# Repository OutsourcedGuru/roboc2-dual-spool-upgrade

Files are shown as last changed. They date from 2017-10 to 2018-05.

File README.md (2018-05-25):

# roboc2-dual-spool-upgrade
Step-by-step instructions for upgrading the Robo C2 for dual filament spools.



## Overview

The Robo C2 printer is awesome in many ways. Its included spool holder, however, has a number of flaws in its design:

* The mounting hole for the spool holder is slightly too large for the included holders, resulting in the holder spinning inside the rectangular hole and sometimes falling out mid-print
* The included holder for 1KG spools really isn't up to the challenge of all that weight
* The holders, as supplied, often catch against Robo's own filament spools given the existing design
* The location of the existing spool holder is too high and too close to the bottom of the filament run-out switch assembly, exacerbating any cross-filament problems and especially with infused rolls

To work around these flaws, I've created a completely new design to accommodate two 1KG spools at once.

The new design includes ball bearings, moves the spool(s) lower, re-orients them so that they're more inline with the filament run-out switch assembly and has a safety feature which helps on Shaxon and other problematically-wound filament spools.

I've decided to create two versions of the holder to include a second *smaller* version to hold two half-KG of filament. The only real difference between the two in printed parts are the lengths of the sleeves and the Under-brackets. And obviously, they use slightly longer dowels. If you like making these, double the amount of ball bearings and bolts and you should be able to make both models easily with the same materials otherwise.

### Follow-up project
Soon enough, I plan to create an enclosure for this dual-spool assembly to keep both spools dry since I intend to print PVA on the second extruder.

## Parts required
I've included pictures below to make this easier.

### Parts to order/buy
* Four non-flanged ball bearings, 8mm ID x 22mm OD, around $1.99 per pair, for [example](https://www.servocity.com/8mm-id-x-22mm-od-non-flanged-ball-bearing)
* Two types of dowel
	* 7/8" x 36", around $3.59 each at arts & crafts stores, for [example](https://www.whiteheadindustrial.com/p-20143-78-x-36-hardwood-dowel-rod-code-brown-no-301621.aspx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)
	* 3/16" x 36", around $0.79 each at arts & crafts stores, for [example](https://www.c2f.com/html/productdetail.asp?p=MID-7905)
* Several types of #6-32 shouldered aluminum bolts, around $1.69 for quantity 25 each for [example](https://www.servocity.com/6-32-zinc-plated-socket-head-machine-screws), or something like [this](https://www.servocity.com/actobotics-hardware-pack-a) would be a better idea
	* 7/16" (11.11mm) @ eight each
	* 1/2" (12.72mm) @ four each
	* 1/4" (6.35) @ two each
* Four or eight soft furniture stick-ons for the bottom
* A 7/64ths hex wrench for tightening all the bolts
* A hammer
* A pocketknife or similar
* A wood or hack saw

ball-bearings

dowel_7-8ths-inch-x-36-inch

dowel_3-16ths-inch-x-36-inch

bolt-6-32_7-16ths

hexkey-7-64ths

### Parts to print
Here's the part list, all in PLA. I used the standard [Robo 3D Jet Black](http://robo.fyi/consumables/filament-by-type-by-vendor) for all the parts.

#### Dual KG version:

1. **RC_DualSpool-1of4(PrintTwice).gcode** x 2 => two **Center Axis Brackets**, two **Center Axis Covers** and four **End Caps**
2. **RC_DualSpool-2of4(PrintOnceKG).gcode** x 1 => two **Assembly** parts and four **Sleeves**
3. **RC_DualSpool-3of4(PrintTwiceKG).gcode** x 2 => two halves of the **Under-brackets** and two **Mid-shims**
4. **RC_DualSpool-4of4(PrintTwiceKG).gcode** x 2 => two halves of the remaining **Under-brackets**

#### Dual Half-KG version:

1. **RC_DualSpool-1of4(PrintTwice).gcode** x 2 => two **Center Axis Brackets**, two **Center Axis Covers** and four **End Caps**
2. **RC_DualSpool-2of4(PrintOnceHalfKG).gcode** x 1 => two **Assembly** parts and four **Sleeves**
3. **RC_DualSpool-3of4(PrintTwiceHalfKG).gcode** x 2 => two halves of the **Under-brackets** and two **Mid-shims**

#### Note
Given that the Robo C2 has a fair degree of inaccuracy when printing Z-oriented holes, it's important for you to print these parts using the GCODE I've provided; otherwise, your bolts won't fit. (I've already factored in the hole-shrinkage in this dimension.)

* Assembly x 2
* End Cap x 4
* Mid-shim x 2 (needs raft & support)
* Sleeve x 4 *{Note that there is a shorter pair for the half-KG version of this project so choose appropriately}*
* Center Axis Bracket x 2
* Center Axis Cover x 2
* Under-bracket (both halves, needs raft & support) x 2 *{Note that there is a shorter pair for the half-KG version of this project so choose appropriately}*

## Installation
After printing all the parts, here are the assembly instructions.

1. Do a test-fit to determine if the **End Caps** fit into the ball bearings; that the 3/16" dowel fits inside the **Sleeves**, **End Caps** and **Mid-shims**; that the #6-32 bolts fit into the threaded holes and fit through the clean ones
2. Use the pocketknife to clean the upper half of the ball bearing slots in both **Assembly** parts
3. Insert one ball bearing each into the related slots in both **Assembly** parts, use a spare raft or other thin plastic part on top of this and use the hammer to gently force them into the back of each hole
4. Add one **End Cap** to each ball bearing
5. Insert the 3/16" dowel into one of the **End Cap** & ball bearing combinations
6. Onto this, thread in this order: one **Sleeve**, one **Mid-shim**, another **Sleeve** and another **End Cap** (with the opposite orientation as the last)
7. Pushing everything together, mark the point where the dowel clears the last part and cut the dowel
8. Repeat for the other ball bearing
9. Sandwich everything together with another **Assembly** part on the opposite side
10. Match up the correct pairs of **Under-brackets**, aligning the holes on the bottom, use two 7/16" bolts to attach them together
11. Flip everything upside-down and begin attaching the combined **Under-brackets** using the four 1/2" bolts... if necessary, carefully use the hammer to set the **Assembly** parts evenly into the rectangular grooves in the **Under-bracket** parts, tighten each bolt firmly
12. Verify that all four sleeves spin freely
13. Add four cushioned furniture bumpers/feet to the bottom to protect your table top
14. Use the 1/4" bolts to attach one each **Center Axis Cover** to the **Center Axis Brackets** (don't over-tighten)
15. Use two each 7/16" bolts to attach both **Center Axis Brackets** to their respective Assembly part, tightening them firmly
16. Close one **Center Axis Cover**, insert the 7/16" dowel through everything and mark a line 2mm inside (the depth of the other **Center Axis Cover**), saw through the dowel
17. Orient the dual-spool holder behind the printer and add two filament spools so that the filament spools clockwise as seen from the right side of the printer, slide the dowel through the middle and close both covers, slightly tightening their bolts by hand

testfit

bottomaxles





sideview-c2andholder



|Donate||Cryptocurrency|
|:-----:|---|:---:|
| eth-receive || btc-receive |
|Ethereum||Bitcoin|

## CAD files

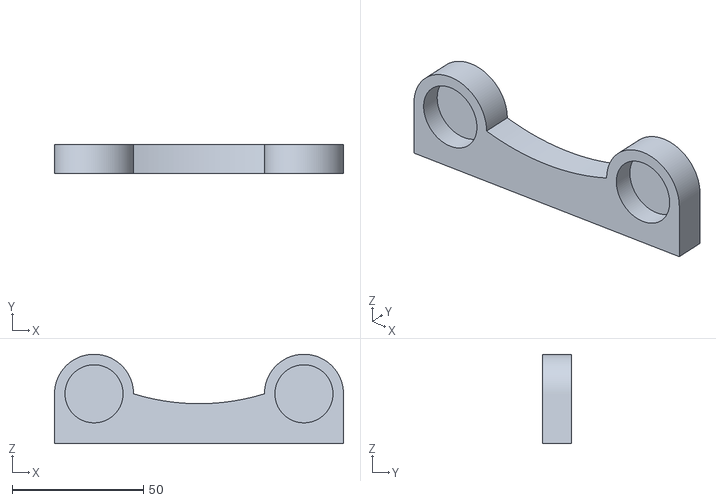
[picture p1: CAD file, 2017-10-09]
parts/stl/DualSpool-Assembly.stl
110.0 x 11.0 x 34.0

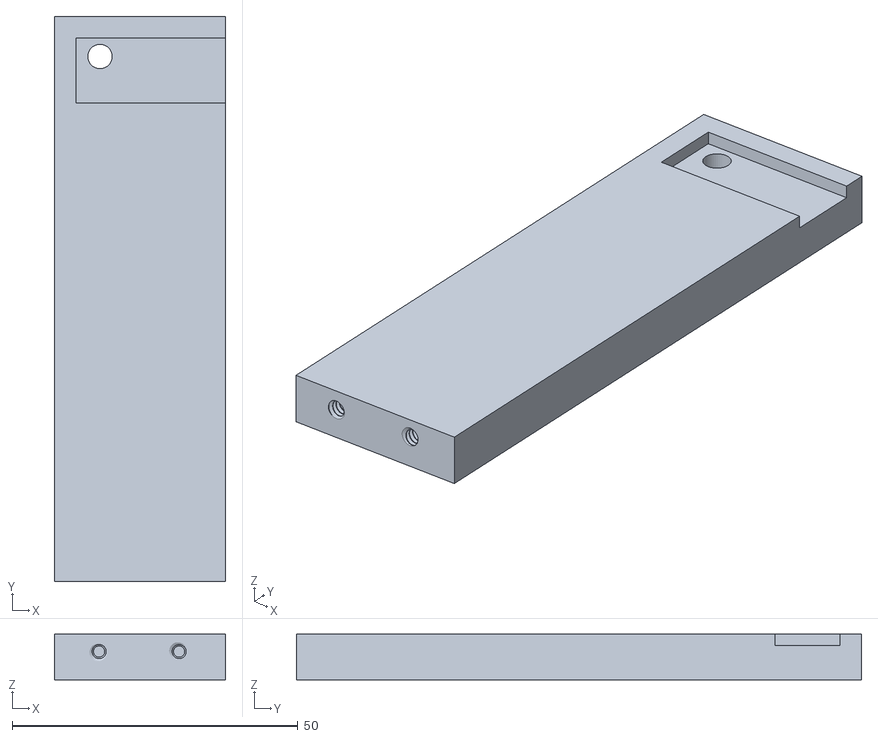
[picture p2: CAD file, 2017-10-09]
parts/stl/DualSpool-UnderBracketFirstHalf_HalfKG.stl
30.0 x 98.9 x 8.00

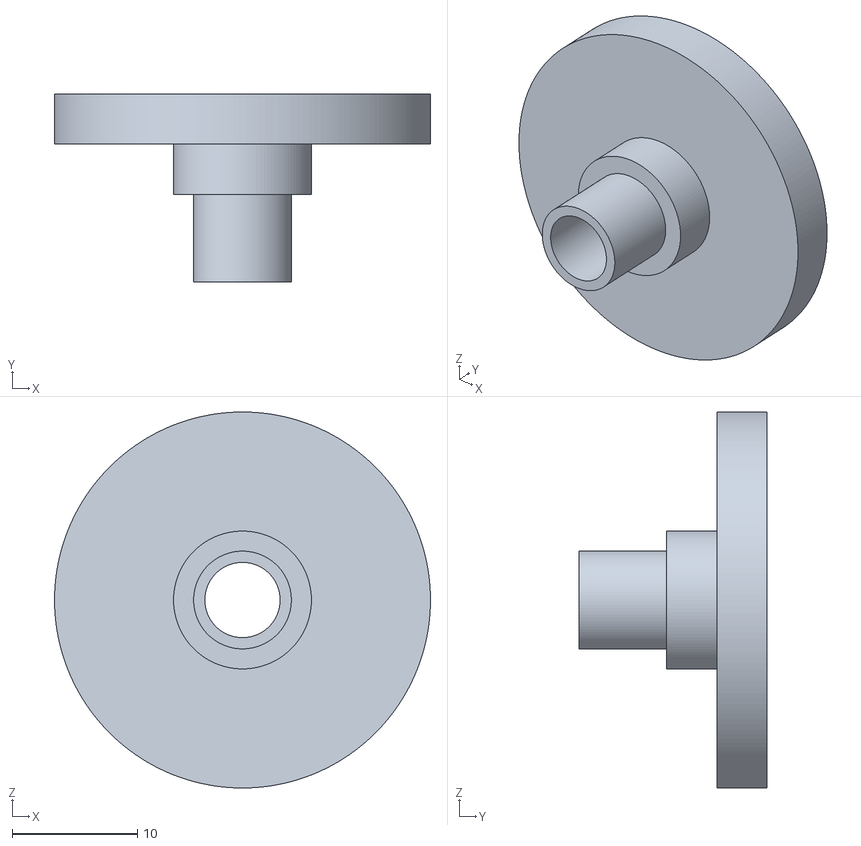
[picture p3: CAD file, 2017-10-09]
parts/stl/DualSpool-EndCap.stl
30.0 x 15.0 x 30.0

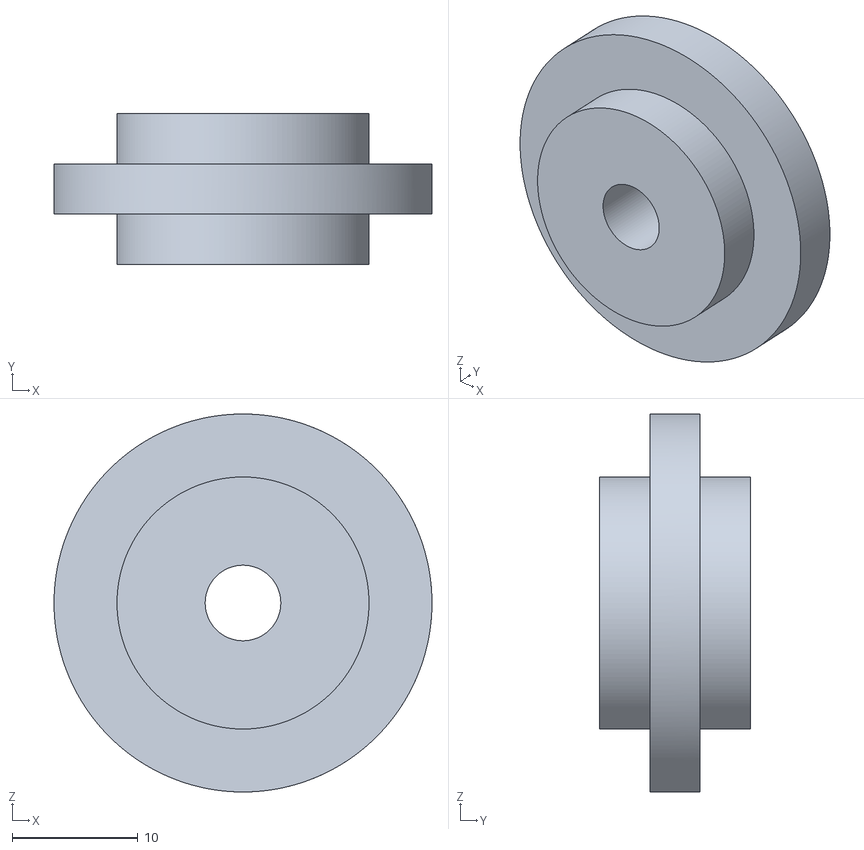
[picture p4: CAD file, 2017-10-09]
parts/stl/DualSpool-MidShim.stl
30.0 x 12.0 x 30.0

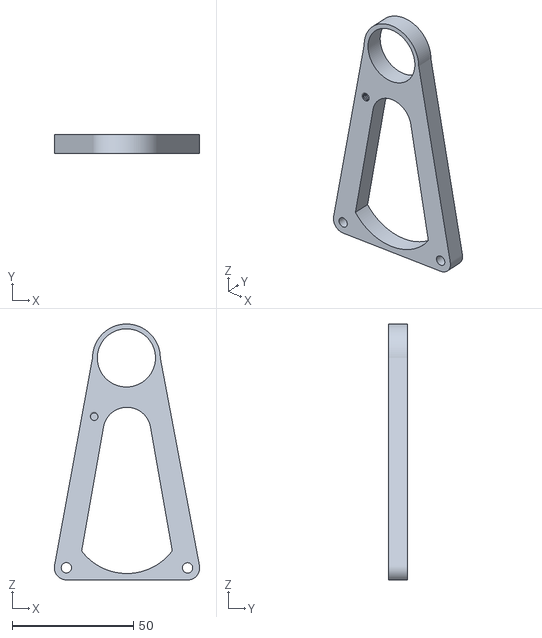
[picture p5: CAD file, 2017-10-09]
parts/stl/DualSpool-CenterAxisBracket.stl
60.0 x 8.00 x 105.7

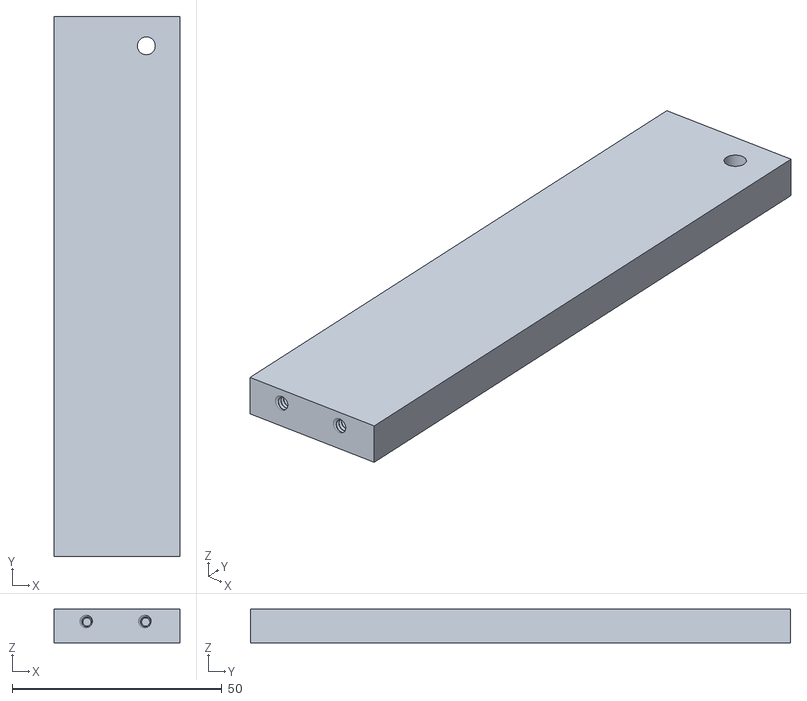
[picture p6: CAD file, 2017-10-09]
parts/stl/DualSpool-UnderBracketFirstHalf_KG.stl
30.0 x 128.9 x 8.00

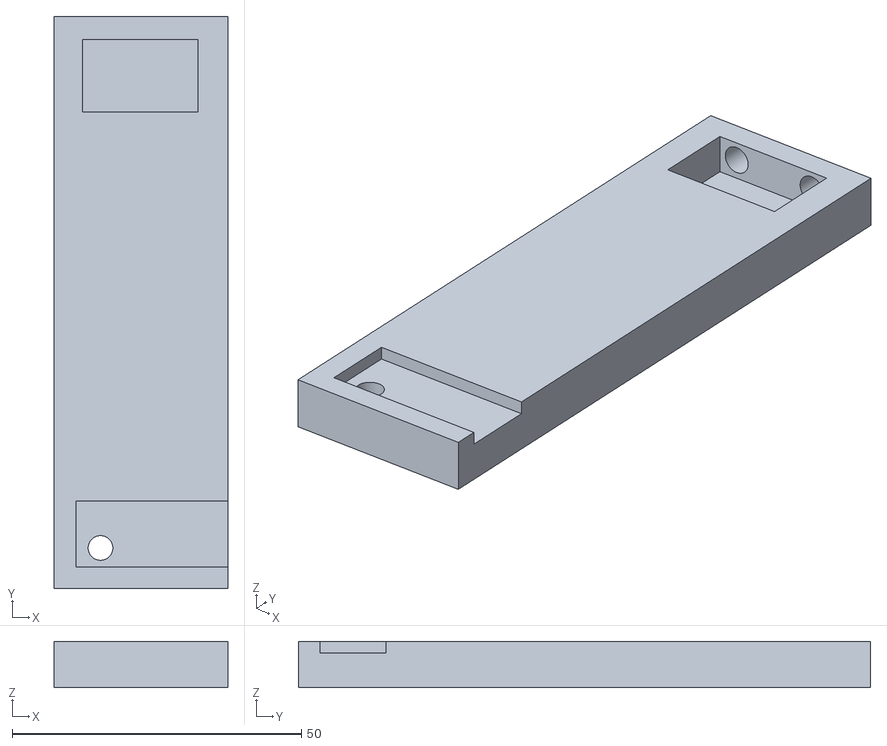
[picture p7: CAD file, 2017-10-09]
parts/stl/DualSpool-UnderBracketSecondHalf_HalfKG.stl
30.0 x 98.9 x 8.00

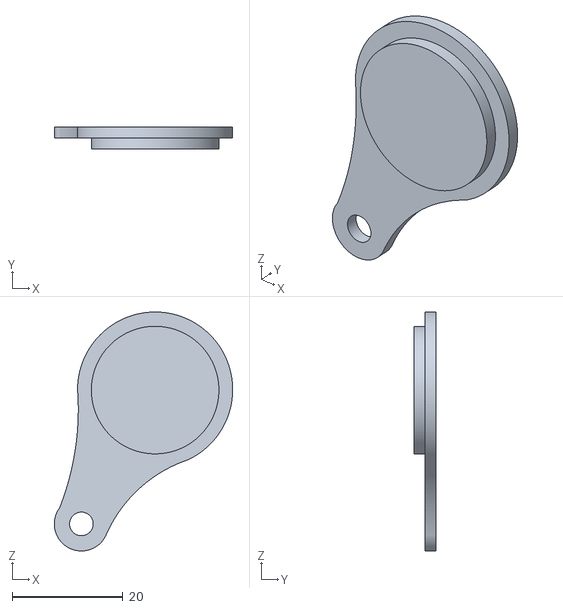
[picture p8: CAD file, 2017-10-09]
parts/stl/DualSpool-CenterAxisCover.stl
32.2 x 4.00 x 43.1

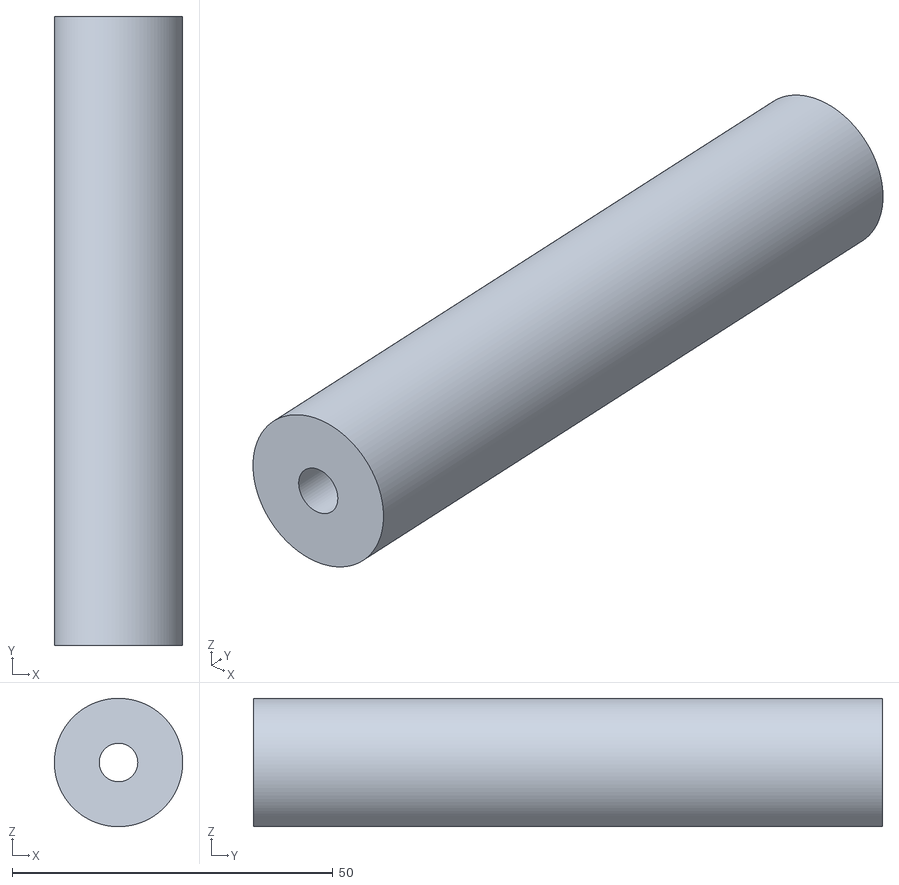
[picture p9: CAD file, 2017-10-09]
parts/stl/DualSpool-SleeveKG.stl
20.0 x 98.0 x 20.0

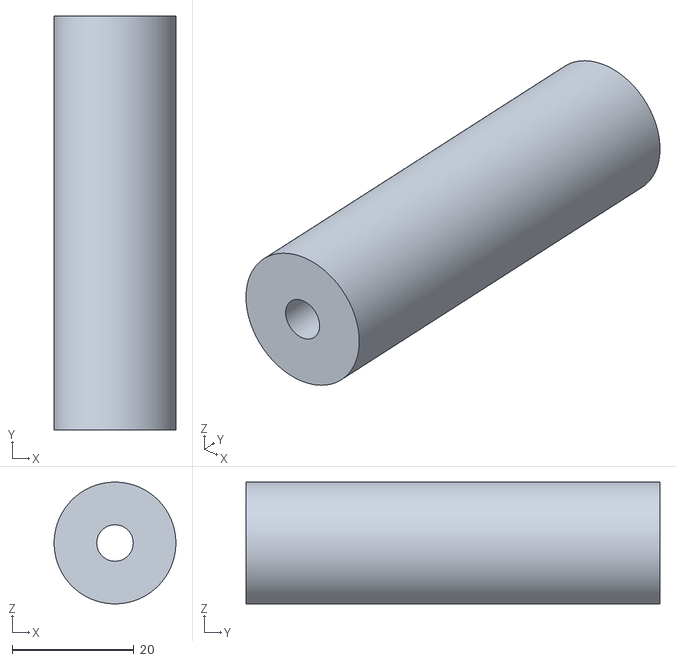
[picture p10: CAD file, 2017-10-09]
parts/stl/DualSpool-SleeveHalfKG.stl
20.0 x 68.0 x 20.0

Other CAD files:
parts/stl/DualSpool-UnderBracketSecondHalf_KG.stl

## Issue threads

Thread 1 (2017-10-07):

Placeholder for README.md images

OutsourcedGuru, 2017-10-07:
7/8" dowel
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

OutsourcedGuru, 2017-10-07:
3/16" dowel
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

OutsourcedGuru, 2017-10-07:
Clamps
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

OutsourcedGuru, 2017-10-07:
#6-32 aluminum bolts
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

OutsourcedGuru, 2017-10-07:
Hex wrench 7/64ths
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

OutsourcedGuru, 2017-10-07:
Ball bearings
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

OutsourcedGuru, 2017-10-08:
Front view, assembled
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

OutsourcedGuru, 2017-10-08:
Front view, without spool or axle
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

OutsourcedGuru, 2017-10-08:
Bottom view
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

OutsourcedGuru, 2017-10-08:
Side view
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

OutsourcedGuru, 2017-10-08:
Side view with C2
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

OutsourcedGuru, 2017-10-08:
Bottom axles
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

OutsourcedGuru, 2017-10-08:
Test fit
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

OutsourcedGuru, 2017-10-11:
Final assembly, KG version
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

Closed 2018-01-20.
